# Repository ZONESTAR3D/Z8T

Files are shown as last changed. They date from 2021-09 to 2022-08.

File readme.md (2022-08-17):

# Z8T Documents
***ATTETION: We have released a new firmware for Z8T, please download it and upload to your printer, please refer to [here](https://github.com/ZONESTAR3D/Firmware/tree/master/Z8/Z8T/ZRIBV6(default)/Firmware/V2.0.0/LCD12864)***
### Download Z8T documents
[**Download all the Z8T documents in one go**](https://downgit.github.io/#/home?url=https://github.com/ZONESTAR3D/Z8T)     
## 0. Readme First
- **Packing list.jpg** Parts list of the Z8T 3D printer DIY kit    
- **Readme First.pdf** Installation and use process of 3D printer DIY Kit  
## 1. User Guide
- **Z8T User Guide-EN(FR/ES/PT/DE/RU).pdf**  Installation and quick user guide  
- **LCD2864 Menu Description.pdf** Menu instruction of 128x64 LCD screen    
- **LCD-DWIN Menu Description.pdf** MENU instruction of 4.3" TFT-LCD screen   
**NOTE**: Default Z8T used a 128x64 LCD screen, if you want to upgrade to a TFT-LCD screen, please refer to this link: [**Z8T upgrade kit**](https://www.aliexpress.com/item/1005002019863241.html)   
- **Z8T Wiring Diagram (ZRIBV6).jpg**  Wiring Diagram for Z8T  
- **TITAN installation tutorial.mp4**  Video tutorial for assemble TITAN extruder  
## 2. Operation Guide 
- [**Mix color HOTEND user guide- load and unload filament.pdf**](https://github.com/ZONESTAR3D/Z8T/blob/main/2.%20Operation%20Guide/Mix%20Color%20HOTEND%20User%20Guide-%20load%20and%20unload%20filament.pdf) Instrution for how to load and unload filament.  
- [**Operature guide for mixing color extruder.pdf**](https://github.com/ZONESTAR3D/Z8T/blob/main/2.%20Operation%20Guide/Operature%20guide%20for%20Mixing%20Color%20Extruder%20V1_3%20-EN.pdf)  Instrution for Operate the Mixing Color Extruder.   
**!!ATETTION!!: Please read these two document if you want to print multi-color 3d prints.**  
- [**Bed auto leveling**](https://github.com/ZONESTAR3D/Upgrade-kit-guide/tree/main/Bed%20Leveling%20Sensor) This directory has instructions on how to do the auto leveling and a leveling test gcode file.    
- **Host software** This directory contains instructions on how to control the 3d printer from PC  
- **Slicing** please click this link to read the newest [**slicing guide**](https://github.com/ZONESTAR3D/Slicing-Guide)  
- **USB driver** Default Z8T used a ZRIB control board, it used a CP2102 USB-UART briges chip, Please download the USB driver from here:
[**CP2012 USB Driver**](https://www.silabs.com/interface/usb-bridges/classic/device.cp2102)   
- **Upgrade features** You can upgrade some features for Z8T:
  - [**32 bits control board**](https://www.aliexpress.com/item/1005001300737027.html) > **Better performance**   
  - [~~**3.5" TFT-LCD with Touch screen**~~](https://www.aliexpress.com/item/1005001314076252.html) > Better UI - **Suggest upgrade to 4.3" TFT-LCD screen**
  - [**4.3" TFT-LCD screen**](https://www.aliexpress.com/item/1005002378065646.html) > **Better UI and easy to use**
  - [**Silent motor driver**](https://www.aliexpress.com/item/4000596369015.html) > **To make the printer more silent and improve printing quality**
  - [**Filament run out detector(FROD)**](https://www.aliexpress.com/item/4001309957376.html)  > **To detect filament run out and pause print**
  - [**3D Touch bed leveling sensor**](https://www.aliexpress.com/item/1005001464420529.html) > **Suit for all types hotbed.**
  - [**ZL-Sensor bed leveling sensor**](https://www.aliexpress.com/item/1005002865311470.html) > **Suit for all types of hotbed and easy to wiring.**
  - [**Hotbed Nuts**](https://www.aliexpress.com/item/4000726717520.html) > **Easy to adjust hot bed height** 
  - [**Magnetic flexible hot bed sticker**](https://www.aliexpress.com/item/4000793898821.html)  > **Pasted firmly and easy to take out**
  - [**Hotbed glass**](https://www.aliexpress.com/item/4001317243160.html) > **Print ABS required**       
  - [**Z lead screw fix module**](https://www.aliexpress.com/item/1005002401708373.html) > **Fix Z lead screws on the profiles**
  - [**The 4th version 3-IN-1-OUT hotend**](https://www.aliexpress.com/item/1005001635908007.html) > **Improve to less string and not easy to be clogged**  
  - [**3-IN-2-OUT hotend**](https://www.aliexpress.com/item/1005001275429959.html) > **make print different types of fialment and mixing feature together**  
  - [**3-IN-3-OUT hotend**](https://www.aliexpress.com/item/1005001275429959.html)  > **Support to print different filament**          
  - [**Upgrade parts combine**](https://www.aliexpress.com/item/1005002019863241.html)  > **Collection of most commonly used upgrade accessories**   
#### Use and installation guide for upgrade features, please refer to [here](https://github.com/ZONESTAR3D/Upgrade-kit-guide)  
- [**Bed Leveling Sensor**](https://github.com/ZONESTAR3D/Upgrade-kit-guide/tree/main/Bed%20Leveling%20Sensor)
	- [**PL-08N**](https://github.com/ZONESTAR3D/Upgrade-kit-guide/tree/main/Bed%20Leveling%20Sensor/Proximity%20Sensor%20(PL-08N))
	- [**ZLSensor**](https://github.com/ZONESTAR3D/Upgrade-kit-guide/tree/main/Bed%20Leveling%20Sensor/ZL-Sensor)
	- [**BLTouch**](https://github.com/ZONESTAR3D/Upgrade-kit-guide/tree/main/Bed%20Leveling%20Sensor/BLtouch(3D%20Touch))
- [**Direct Drive Extrruder**](https://github.com/ZONESTAR3D/Upgrade-kit-guide/tree/main/Direct%20Drive%20Extrruder)
- [**Filament run out sensor**](https://github.com/ZONESTAR3D/Upgrade-kit-guide/tree/main/FROD)
- [**HOTEND**](https://github.com/ZONESTAR3D/Upgrade-kit-guide/tree/main/HOTEND)
	- [**M2 2_IN-1-OUT Mixing Color Hotend**](https://github.com/ZONESTAR3D/Upgrade-kit-guide/tree/main/HOTEND/M2%202_IN-1-OUT%20Mixing%20Color%20Hotend)
	- [**M2P1 3-IN-2-OUT Mixing Color Hotend**](https://github.com/ZONESTAR3D/Upgrade-kit-guide/tree/main/HOTEND/M2P1%20%203-IN-2-OUT%20Mixing%20Color%20Hotend)
	- [**R3 3-IN-3-OUT HOTEND**](https://github.com/ZONESTAR3D/Upgrade-kit-guide/tree/main/HOTEND/R3%203-IN-3-OUT%20HOTEND)
	- [**M3 3-IN-1-OUT Mixing Color Hotend**](https://github.com/ZONESTAR3D/Upgrade-kit-guide/tree/main/HOTEND/M3%20%203-IN-1-OUT%20Mixing%20Color%20Hotend)
	- [**E4 4-IN-1-OUT Non-Mixing Color Hotend**](https://github.com/ZONESTAR3D/Upgrade-kit-guide/tree/main/HOTEND/E4%204-IN-1-OUT%20Non-Mixing%20Color%20Hotend)
	- [**M4 4-IN-1-OUT Mixing Color Hotend**](https://github.com/ZONESTAR3D/Upgrade-kit-guide/tree/main/HOTEND/M4%20%204-IN-1-OUT%20Mixing%20Color%20Hotend)	
- [**Laser Engraving Kits**](https://github.com/ZONESTAR3D/Upgrade-kit-guide/tree/main/Laser%20Engraving)
- [**Stepping motor drivers**](https://github.com/ZONESTAR3D/Upgrade-kit-guide/tree/main/Motor%20Drive%20Module)
- [**TFT-LCD screens**](https://github.com/ZONESTAR3D/Upgrade-kit-guide/tree/main/TFT-LCD)
	- [**3.5" TFT-LCD screen**](https://github.com/ZONESTAR3D/Upgrade-kit-guide/tree/main/TFT-LCD/TFTLCD35-MK)
	- [**4.4" TFT-LCD screen**](https://github.com/ZONESTAR3D/Upgrade-kit-guide/tree/main/TFT-LCD/LCD-DWIN)  
- [**WiFi wireless controller**](https://github.com/ZONESTAR3D/Upgrade-kit-guide/tree/main/WiFi)  
## 3. Test gcode
Inlcuded some gcode files for testing.  
## 4. TroubleShootings
Inlcuded some TroubleShootings files. 
## 5. Print Parts
Inlcuded the print parts stl fils for Z8T.
## 6. Firmware 
- [**Default firmware hex file**](https://github.com/ZONESTAR3D/Firmware/tree/master/Z8/Z8T/ZRIBV6(default)/Firmware/V2.0.0/LCD12864)     
- [**More Firmware hex file**](https://github.com/ZONESTAR3D/Firmware/tree/master/Z8/Z8T)  
- [**Firmware Upload tool (for windows)**](https://github.com/ZONESTAR3D/Firmware/tree/master/Firmware_Upload_tool_for_ZRIB_ZMIB)   
**NOTE: if you use macos and linux, please upload firmware by Cura**   
- [**Firmware sourc code**](https://github.com/ZONESTAR3D/source-code-for-3d-printer)

## How to downlod files from Github page
#### Step 1: Click this link [**https://downgit.github.io/**](https://downgit.github.io/) 
#### Step 2: Copy the Github file or direcotry link which you want to download.
#### Step 3: Click download button and wait a few seconds, it will start to download automatically. 


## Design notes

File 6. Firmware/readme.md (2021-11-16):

# firmware hex file
- please download from here: https://github.com/ZONESTAR3D/Firmware/tree/master/Z8/Z8T

# firmware source code
- please download from here: https://github.com/ZONESTAR3D/source-code-for-3d-printer

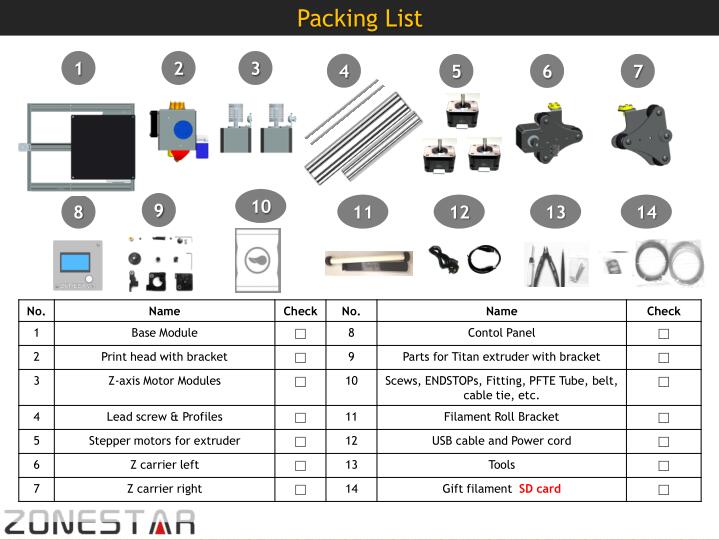
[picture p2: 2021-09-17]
0. Readme First/Packing List.jpg

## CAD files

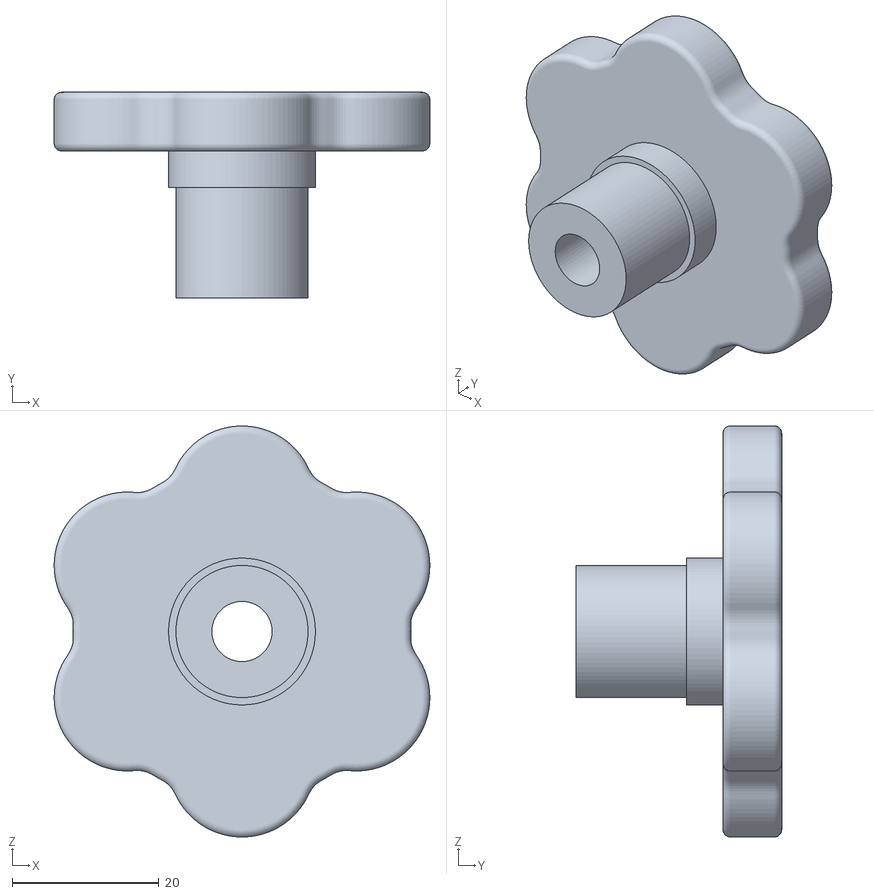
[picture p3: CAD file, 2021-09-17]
5. Print Parts/ls-cap.stl
51.2 x 28.0 x 56.0

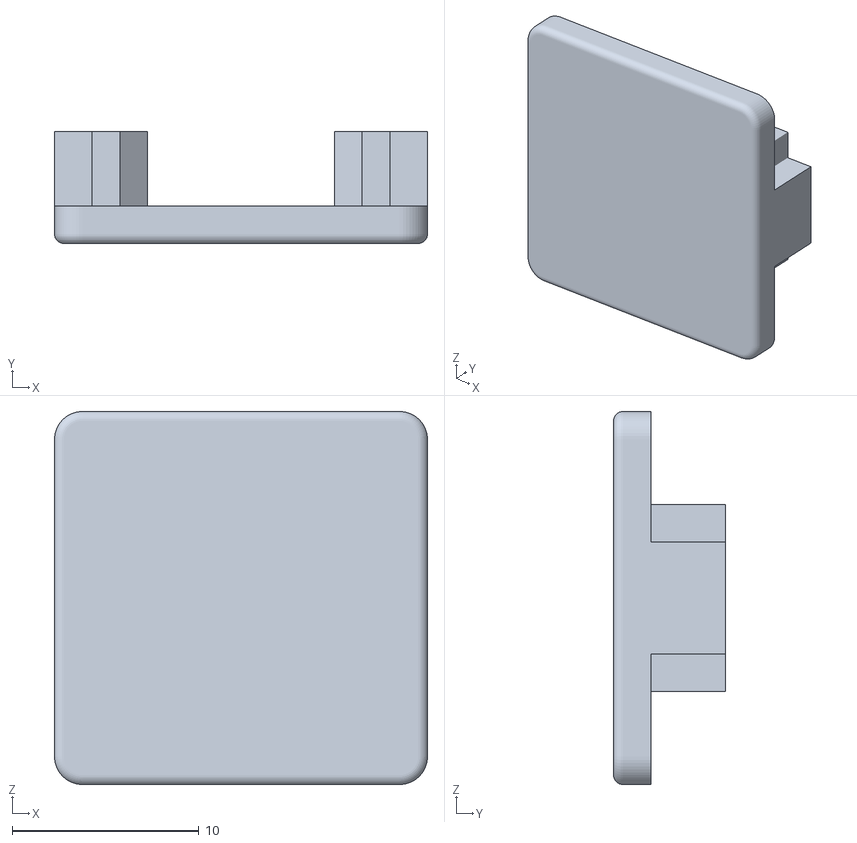
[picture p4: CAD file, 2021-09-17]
5. Print Parts/cap_af_20v.stl
20.0 x 6.00 x 20.0

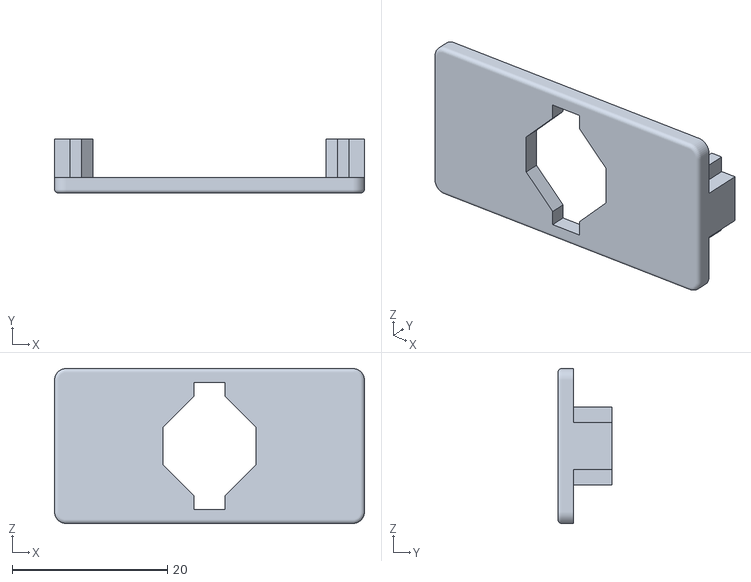
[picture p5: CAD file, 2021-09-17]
5. Print Parts/cap_af_40v.stl
40.0 x 7.00 x 20.0

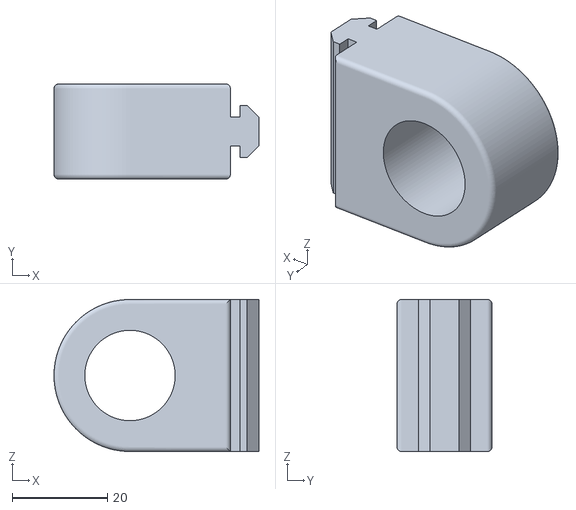
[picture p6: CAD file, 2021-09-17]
5. Print Parts/ls_hold.stl
43.1 x 20.0 x 32.0

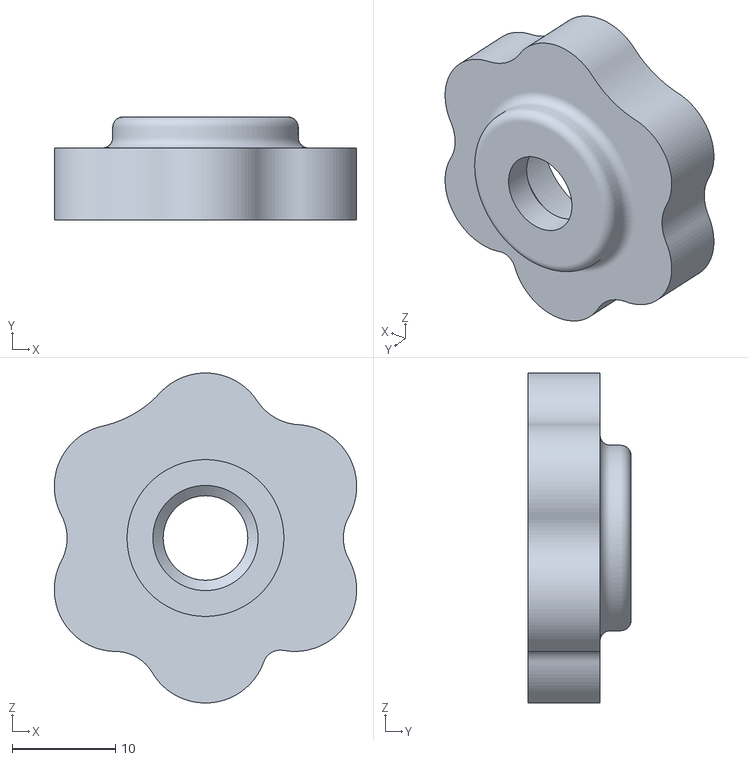
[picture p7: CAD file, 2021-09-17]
5. Print Parts/cap_m4nut.stl
29.3 x 10.0 x 32.0

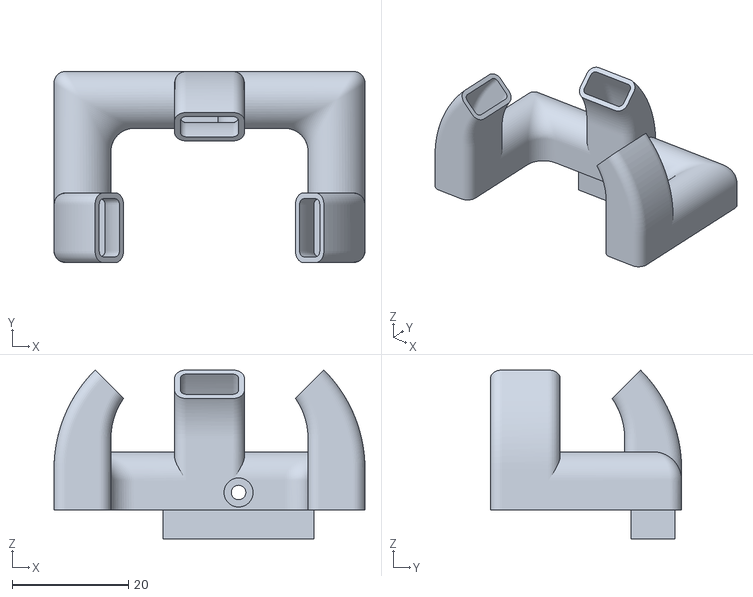
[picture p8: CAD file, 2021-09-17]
5. Print Parts/fanduck_m3_v4.stl
53.5 x 32.9 x 29.1

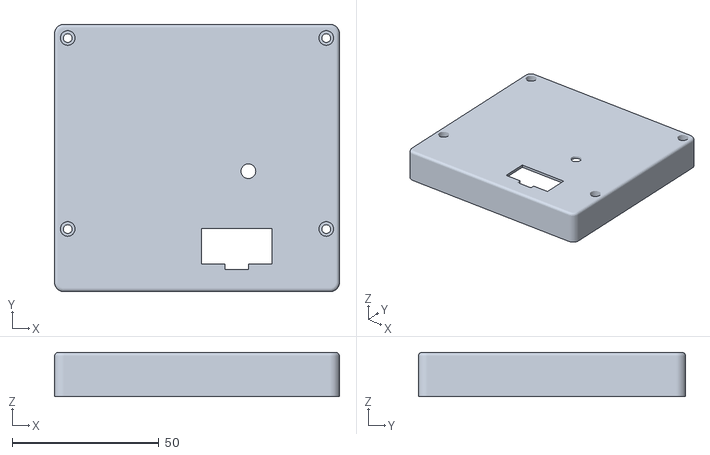
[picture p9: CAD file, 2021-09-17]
5. Print Parts/lcd12864_case_v2.stl
97.0 x 91.0 x 15.0

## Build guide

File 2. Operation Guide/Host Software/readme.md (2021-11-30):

If you want to control your 3d printer from PC, we recommend you choose repetier-host.  
[**Download Repetier host**](https://www.repetier.com/download-software/)
About how to use Repetier Host, please refer to "**Repetier Host User Guide V1.pdf**", more detail guide, please refer to [**Repetier-Host user guide**](http://www.repetier.com/documentation/repetier-host/)

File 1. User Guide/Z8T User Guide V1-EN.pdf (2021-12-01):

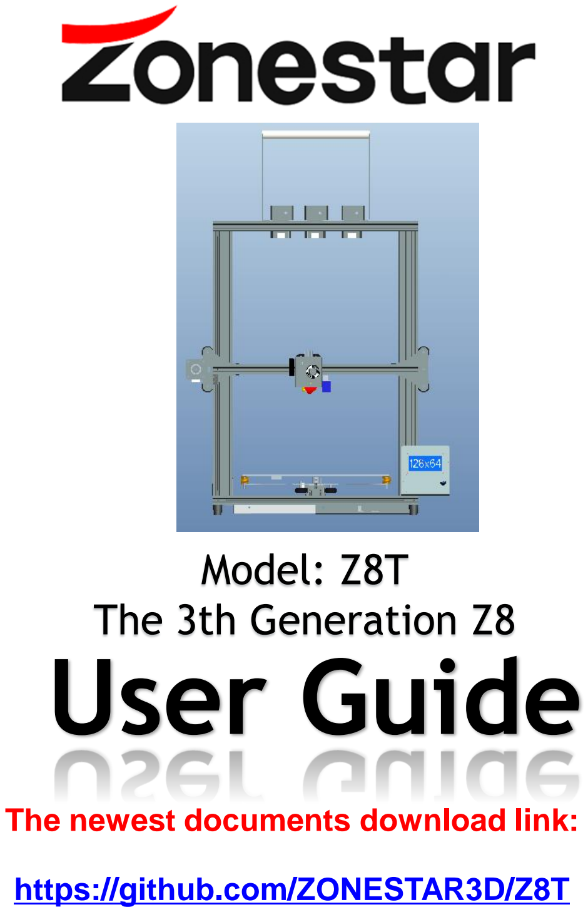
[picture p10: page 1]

# Model: Z8T The 3th Generation Z8

# User Guide

## The newest documents download link:

## https://github.com/ZONESTAR3D/Z8T

1、Nozzle diameter： | 0.4mm
2、Nozzle temperature: | 260℃max
3、Hotbed temperature: | 115℃max
3、Filament diameter： | 1.75mm
4、Print layer thickness: | 0.1~0.3mm(recommend 0.2mm)
5、Filament type: | PLA/ABS/PETG etc.
6、Slicing software： | Cura/Repetier-Host/Simplify3D
7、Interface mode： | USB/SD-Card
8、Power specifications： | Input: 100VAC or 240VAC,50/60Hz
| Output: 24V,15A
9、Print size： | 300(X)*300(Y)*400(Z)mm
10、Gross weight： | 12Kg
11、Environment temperature: | 5~40℃

# Symbols

•Extruder:
The system to carry out Feeding-Melting-Stacking in FDM 3d printer. •Extrusion feeder:
A mechanism to transport filament to the hot end.
•Titan Extruder:
A special remote extrusion feeder with deceleration structure, it can reduce the torque requirements in the stepper motor. •3D printer filament:
In order to facilitate the work of 3D printer, plastic materials are pre processed into filaments. The commonly used types include PLA, ABS, PETG, TPU, PC, AAS, HIPS, PVA, WOOD, Carbon Fiber, etc..
•Hotend:
The part to melt the filament.
•Nozzle:
The outlet at the front end of the HOTEND, usually made of copper and has a small size hole for flow out filament. •Print head:
It means the Hotend and its attached cooling system.
•Printing platform:
The device supporting the printed object.
•Hotbed:
Heatable printing platform.
•Sticker (of hotbed):
A special stickers pasted on the Hotbed are usually made of high temperature adhesive tape or PC film. •Bed Automatic leveling:
A function of automatically measuring and adjusting the distance between nozzle and printing platform. •Control panel:
The system that realizes human-machine interface in 3D printer.
•CoreXY:
A special motion structure with two motors and belt to drive the X-axis and Y-axis together, it is appiled in Z9M3. •Motor Driver Module:
An electronic function module to drive stepper motor.
•Mixer:
The parts and software to realize the color mixing function.
•HOTEND Clean tool:
A screw with a small rod which can be used to clean the feeding channel at the hot end or close the unused channel.

Please put the printer away from the reach of kids.

Must be guided by adults when children are installed or used.

Take care when installation, to avoid electrical shock hazards.

## Please keep well-ventilated condition! May produce toxic gases when

printer working.

## Caution: Hot!

Hotend has high temperature even the printer stop working.

## Caution: Hot!

Hotbed has high temperature even the printer stop working.

Please strictly follow the standard operation when installation.

## Please make sure you have set the AC power select switch to the

correct position before power on.

## For mixing color printer, must load filament to all of the extruders or use hotend clean tool to close the unused channel, even if you print

single color 3D object.
4

# Packing List

1 | 2 | 3 | 4 | 5 | 6 | 7

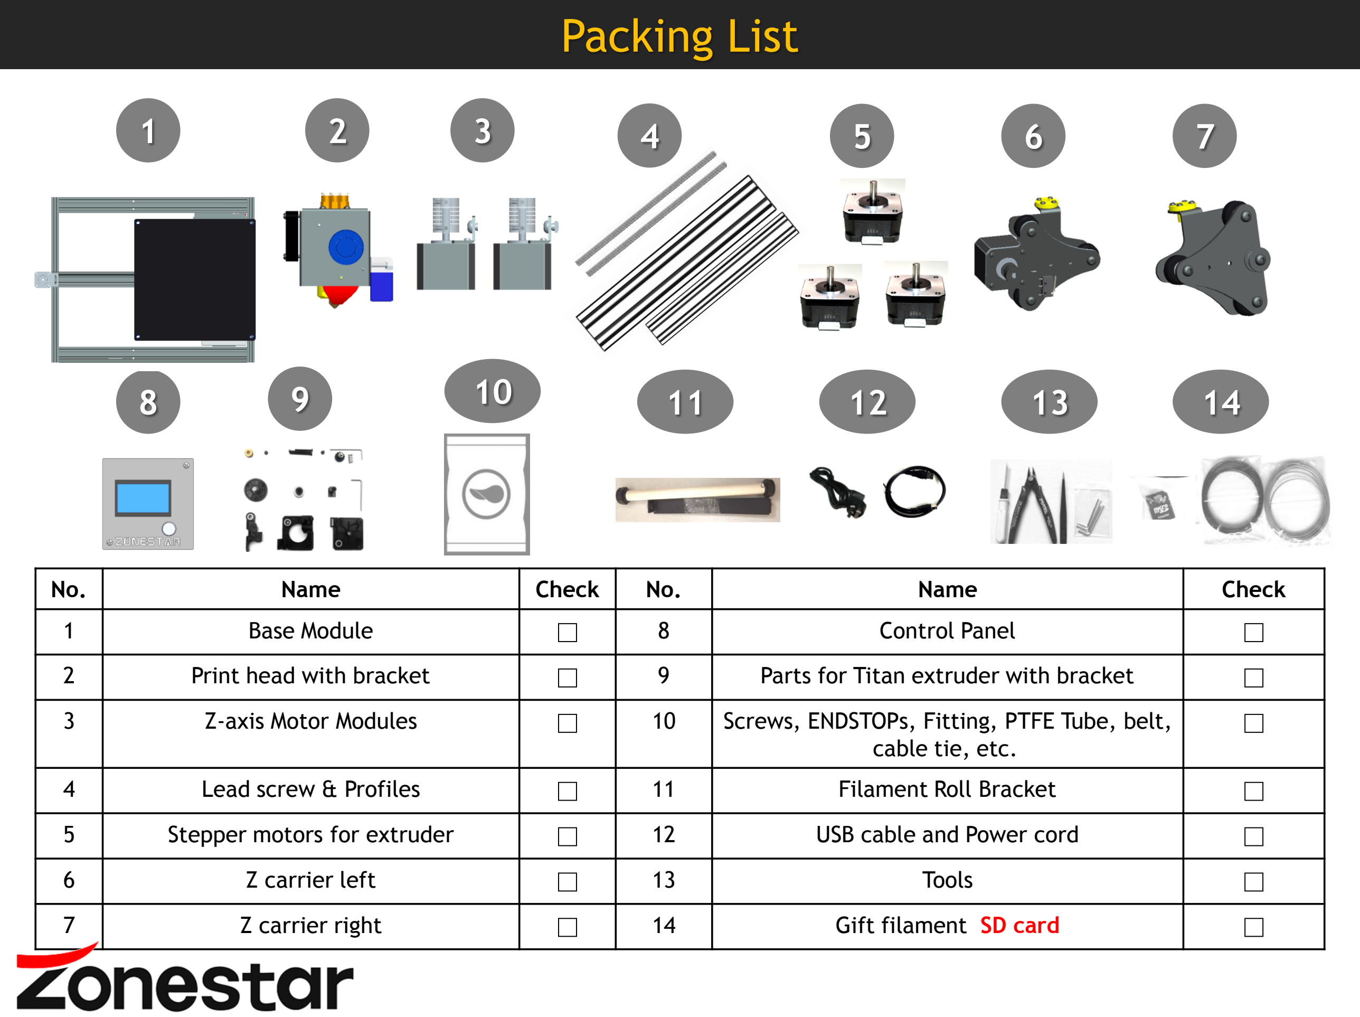
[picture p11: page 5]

No. | Name | Check | No. | Name | Check
1 | Base Module | □ | 8 | Control Panel | □
2 | Print head with bracket | □ | 9 | Parts for Titan extruder with bracket | □
3 | Z-axis Motor Modules | □ | 10 | Screws, ENDSTOPs, Fitting, PTFE Tube, belt, cable tie, etc. | □
4 | Lead screw & Profiles | □ | 11 | Filament Roll Bracket | □
5 | Stepper motors for extruder | □ | 12 | USB cable and Power cord | □
6 | Z carrier left | □ | 13 | Tools | □
7 | Z carrier right | □ | 14 | Gift filament SD card | □

8 14

9 | 11 | 12 | 13 10

# Assemble Titan Extruder (3 sets)

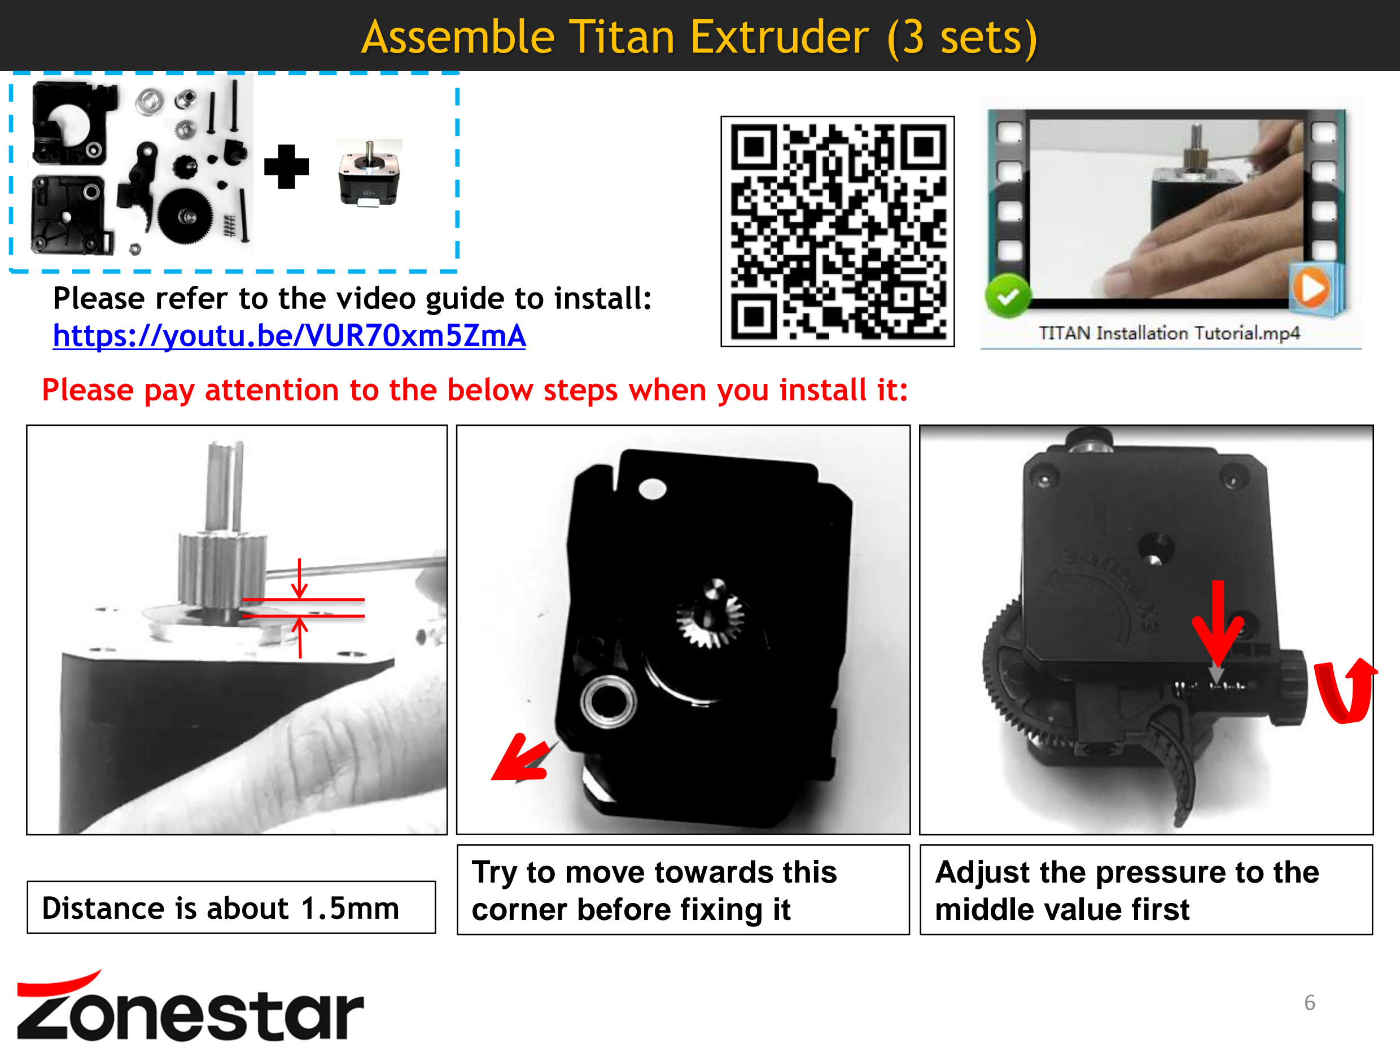
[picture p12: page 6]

## Please refer to the video guide to install: https://youtu.be/VUR70xm5ZmA

## Please pay attention to the below steps when you install it:

## Try to move towards this Distance is about 1.5mm corner before fixing it

## Adjust the pressure to the middle value first

# Install Z axis Parts

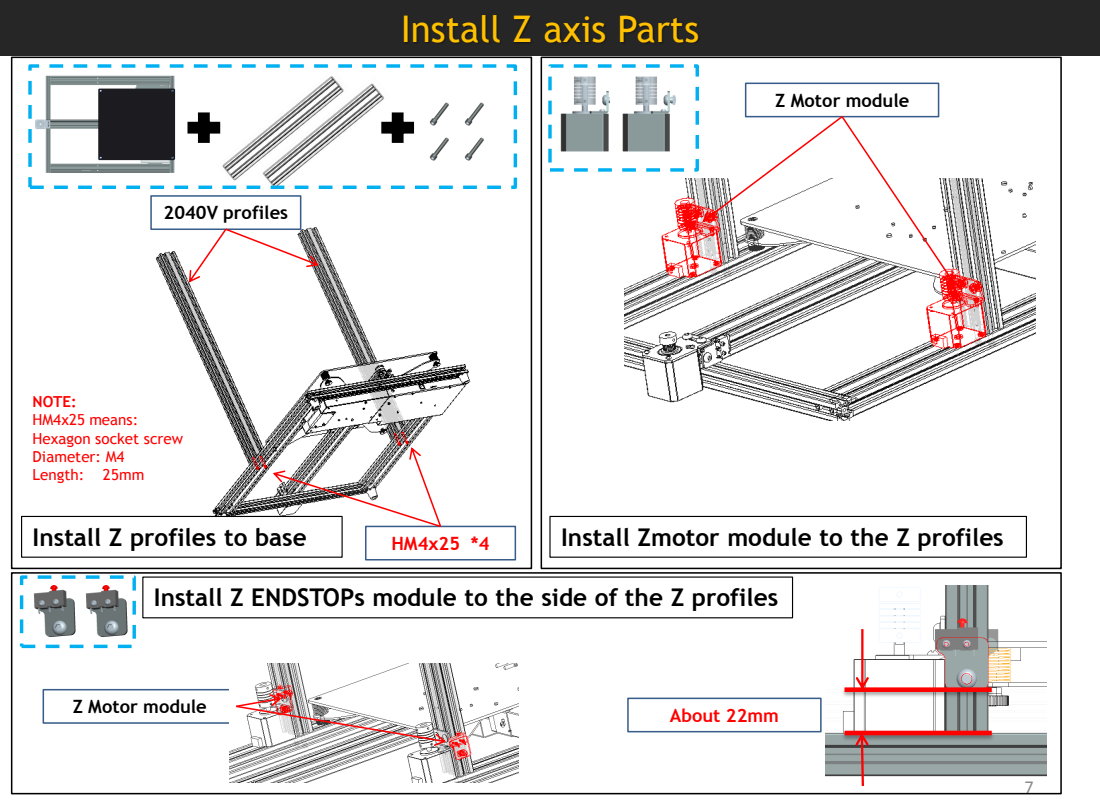
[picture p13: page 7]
2040V profiles; Z Motor module; About 22mm; Length:

NOTE:
HM4x25 means:
Hexagon socket screw
Diameter: M4

Install Z profiles to base

Install Zmotor module to the Z profiles

Install Z ENDSTOPs module to the side of the Z profiles

# Install Z axis Parts

Install Z silders | Install lead screws

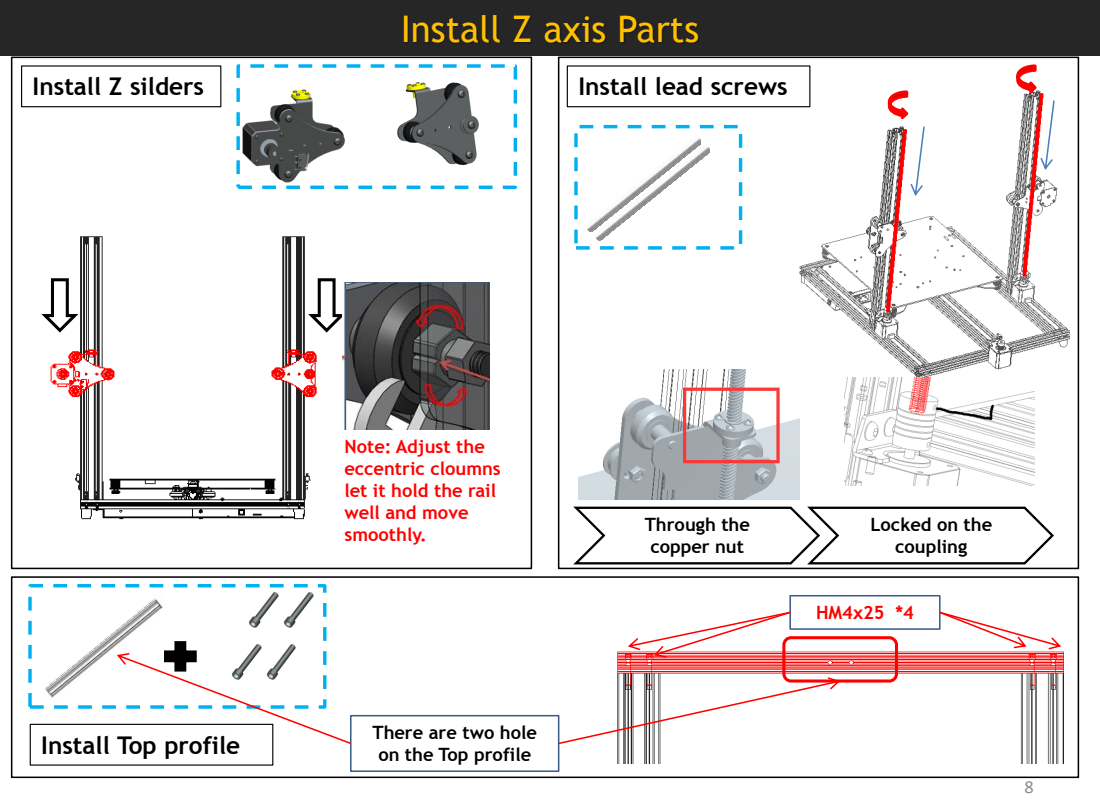
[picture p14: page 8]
Through the copper nut

Note: Adjust the
eccentric cloumns
let it hold the rail
well and move
smoothly.

Locked on the
coupling

There are two hole
on the Top profile

Install Top profile

# Install X axis Parts

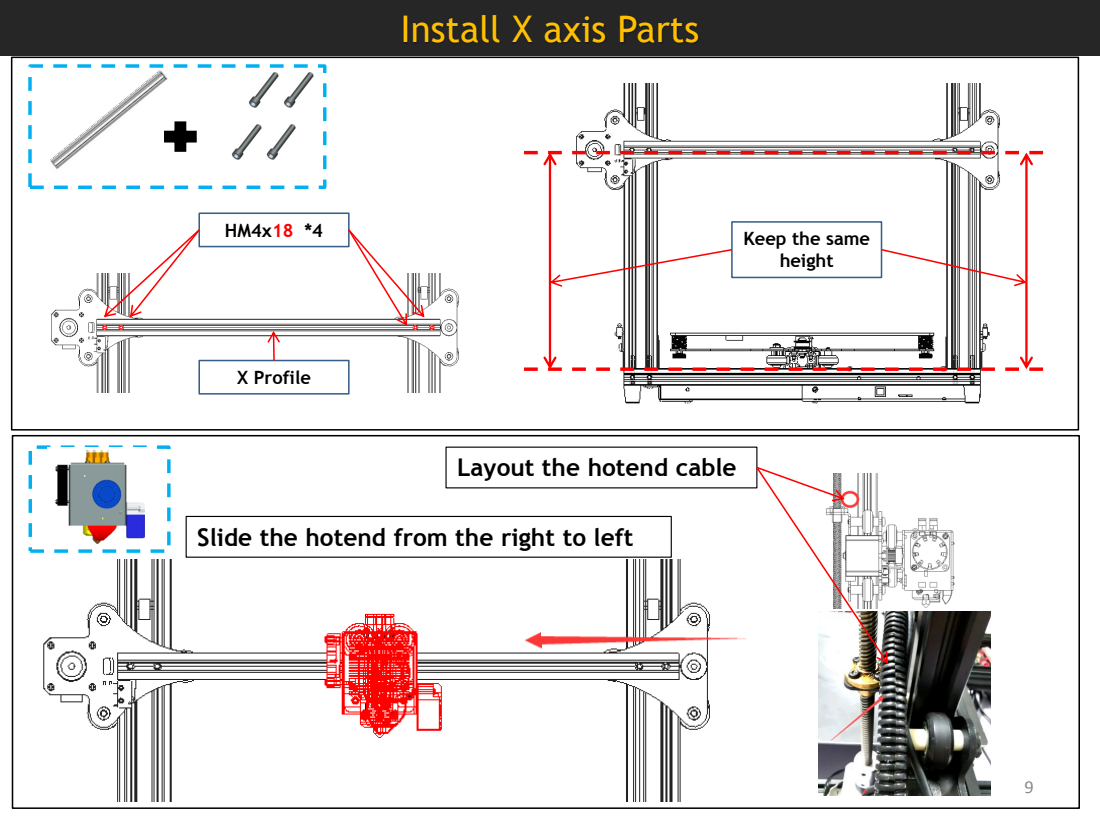
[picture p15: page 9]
X Profile

Keep the same
height

Layout the hotend cable

Slide the hotend from the right to left

# Install X belt

## Install the X belt

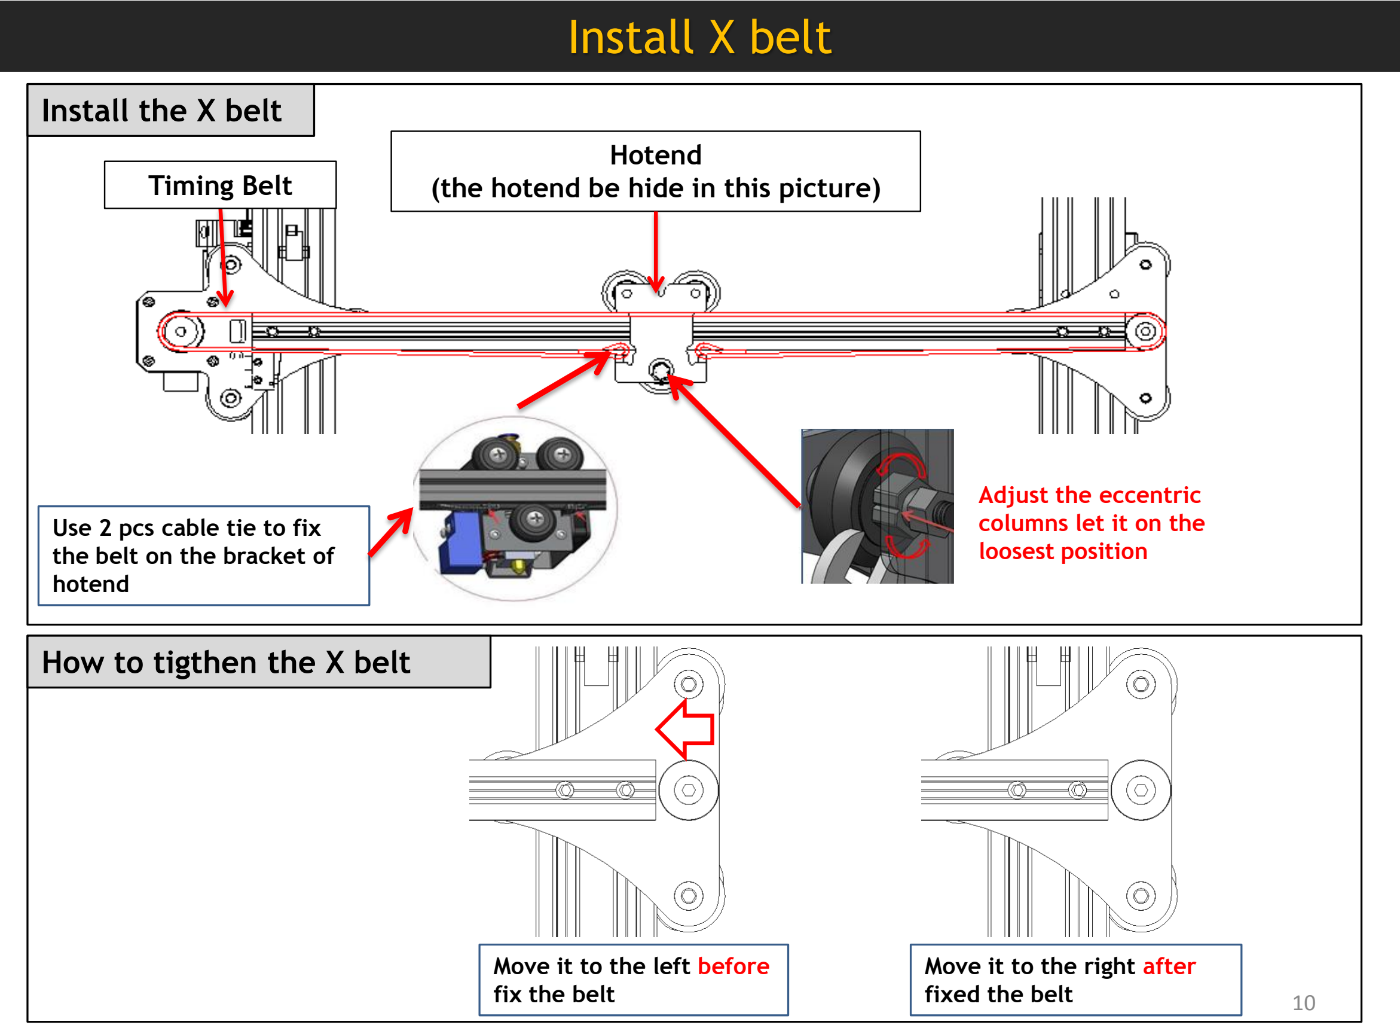
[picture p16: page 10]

Timing Belt

Hotend
(the hotend be hide in this picture)

Adjust the eccentric
columns let it on the
loosest position

Use 2 pcs cable tie to fix the belt on the bracket of hotend

Move it to the left before fix the belt

Move it to the right after fixed the belt

## How to tigthen the X belt

# Install the other parts

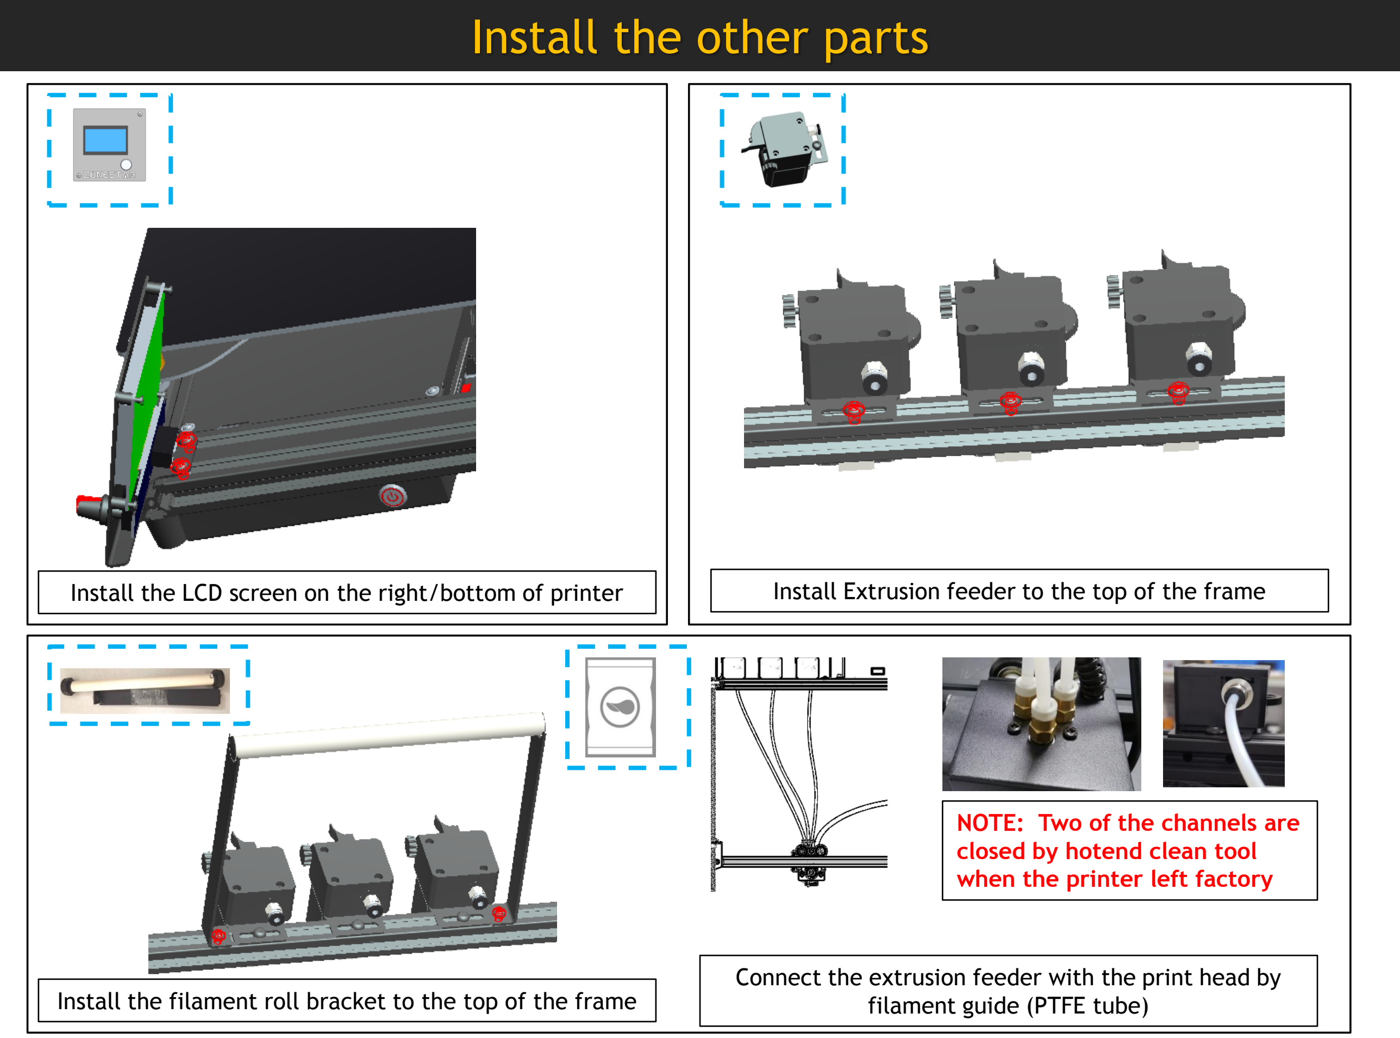
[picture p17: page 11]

Install the LCD screen on the right/bottom of printer | Install Extrusion feeder to the top of the frame

Install the filament roll bracket to the top of the frame

Connect the extrusion feeder with the print head by filament guide (PTFE tube)

NOTE: Two of the channels are closed by hotend clean tool when the printer left factory

# Adjust height of Z ENDSTOPs

## Step 1: Adjust the 4 hand nuts under the hotbed, let the hotbed is parallel with bottom

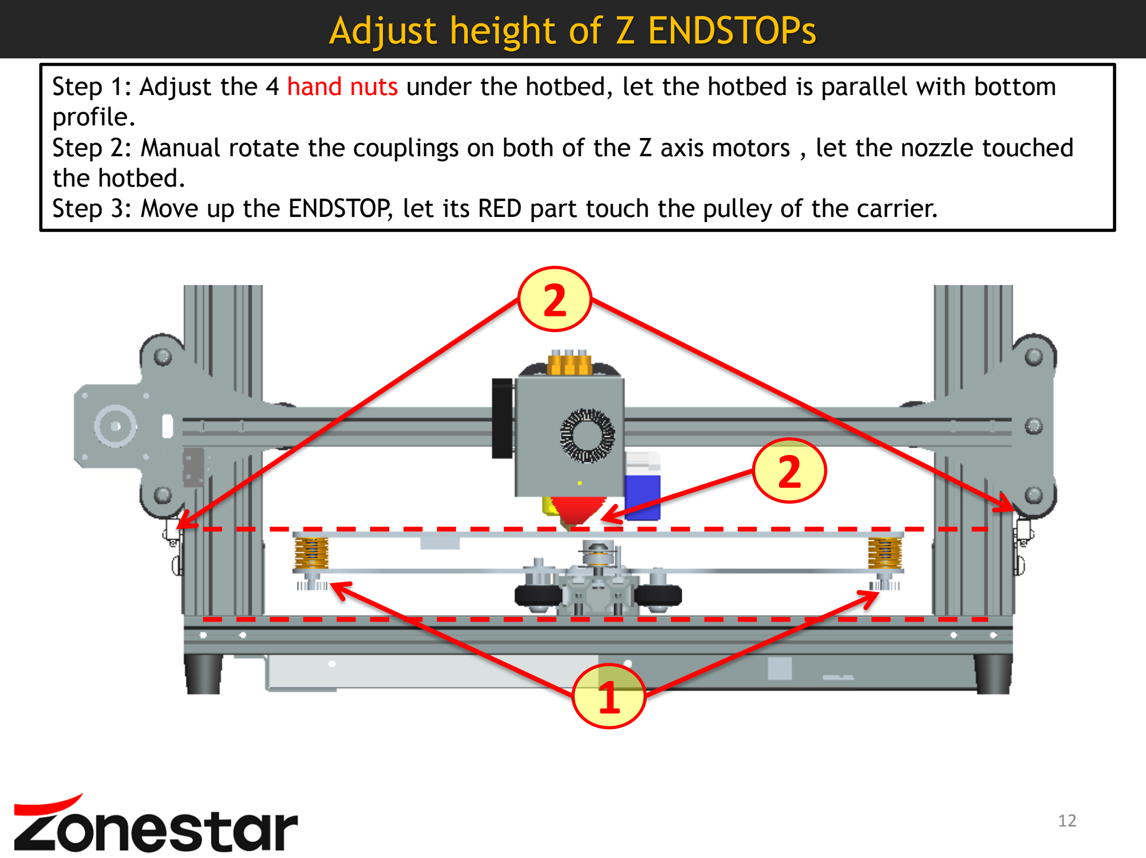
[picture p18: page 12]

profile.

## Step 2: Manual rotate the couplings on both of the Z axis motors , let the nozzle touched

the hotbed.
Step 3: Move up the ENDSTOP, let its RED part touch the pulley of the carrier.

1

2

2

# !!ATTENTION!!

## Take care when installation, to avoid electrical shock hazards!

## Double check the wiring! WRONG WIRING MAY DAMAGED THE ELECTRONIC DEVICE!

## Set the 110V/220V swicth (on the side of power supply) to correct position according to your city power voltage!

## Put the motor wire to the grooves of profile and cover them by

plastic profile cover, and using cable tie to wrap the free wires.

## Stop working immediately if the motor has abnormal vibration or noise,, otherwise the driver modules may be damaged!

## Make sure the hotend cooling fan is working when the nozzle

temperature is over 60 degree, otherwise check the wiring again.

## DC-IN, HOTBED has lager operating current, please make sure

these wires contact well with the terminal.

Step 4: Manually move the hotend and hotbed to see if the movement is smooth, otherwise,

## adjust the eccentric nut until the motor moves smoothly. Refer to the installation

procedure.

## Step 3: Move the hotend and hotbed to their respective limit switch positions to check whether the contact is good and there is a clear sound. Otherwise, please check the limit

switch and reassemble it.

## Step 7: Manually rotate the z-axis screw rod to check whether the z-axis limit switch

contacts reliably.

Step 5: Check whether the X and Y-axis drive belt is firmly installed. If it is too loose, please try to tighten it.

## It is very important to check the machine before power on. It can eliminate the trouble brought by some hardware to ensure the smooth printing!

## Step 6: Check whether the screw rod is assembled in place and whether the screw is tightened

Step 1:Please check if the X&Y axis timing pulley are fixed on the shaft of motor, and the couplings are fixed on the shaft of the Z motors.
Step 2:Please check if the lead screws have been fixed on the shaft of coupling.

# About electronics parts

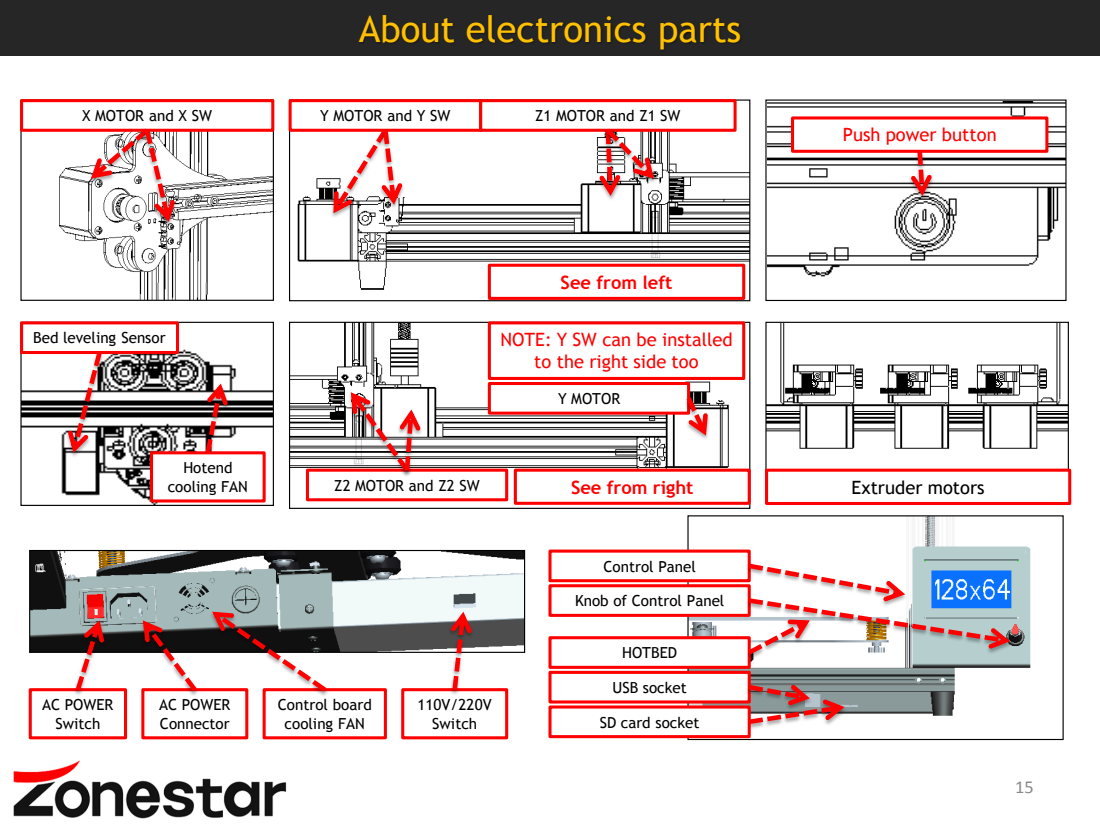
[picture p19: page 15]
X MOTOR and X SW; Y MOTOR and Y SW; Z1 MOTOR and Z1 SW; Extruder motors; Hotend; cooling FAN; Z2 MOTOR and Z2 SW; Y MOTOR; AC POWER Switch; AC POWER Connector; Control board cooling FAN; 110V/220V Switch

Push power button

See from left

Bed leveling Sensor

NOTE: Y SW can be installed
to the right side too

See from right

Control Panel

Knob of Control | Panel

HOTBED

USB socket

SD card socket

# Wiring photos

## Before power on, please open the control box and double check the wiring:

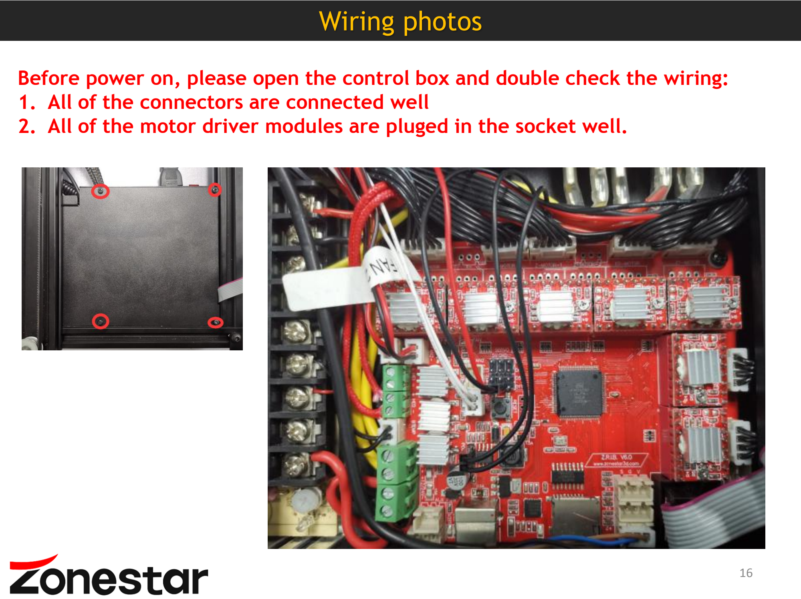
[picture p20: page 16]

## 1. All of the connectors are connected well

2. All of the motor driver modules are pluged in the socket well.

# Wiring Diagram

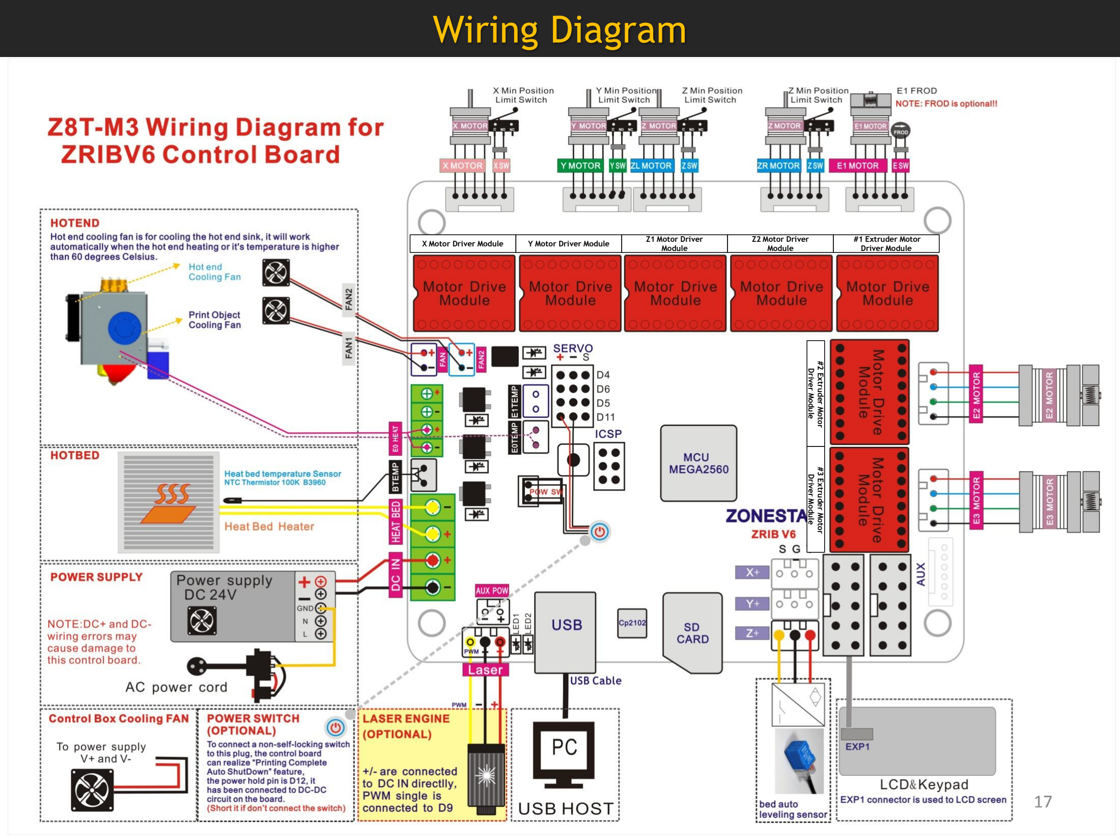
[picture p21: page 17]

X Motor Driver Module | Y Motor Driver Module | Z1 Motor Driver Module

Z2 Motor Driver
Module

#1 Extruder Motor

Driver Module

#2 Extruder Motor

Driver Module

#3 Extruder Motor

Driver Module

# Layout the wires / cables

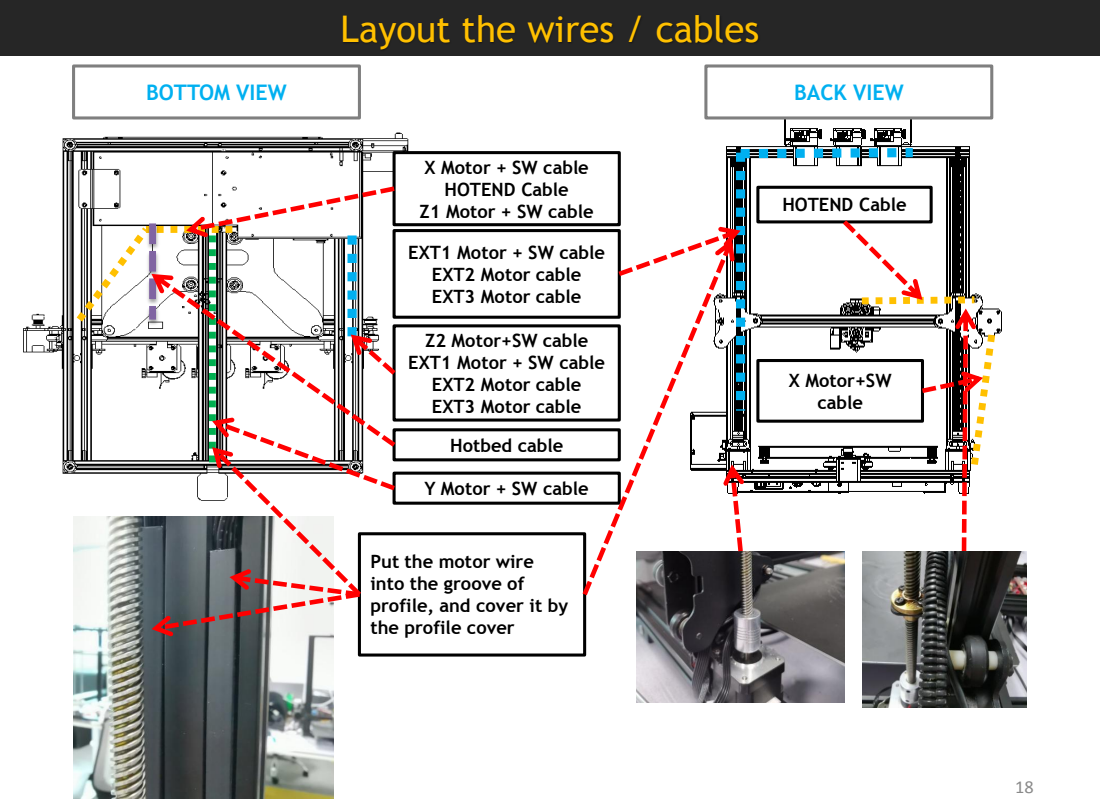
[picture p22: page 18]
Hotbed cable; BOTTOM VIEW; BACK VIEW; HOTEND Cable; X Motor+SW cable

X Motor + SW cable
HOTEND Cable
Z1 Motor + SW cable

EXT1 Motor + SW cable
EXT2 Motor cable
EXT3 Motor cable

Z2 Motor+SW cable

Y Motor + SW cable

Put the motor wire
into the groove of
profile, and cover it by
the profile cover

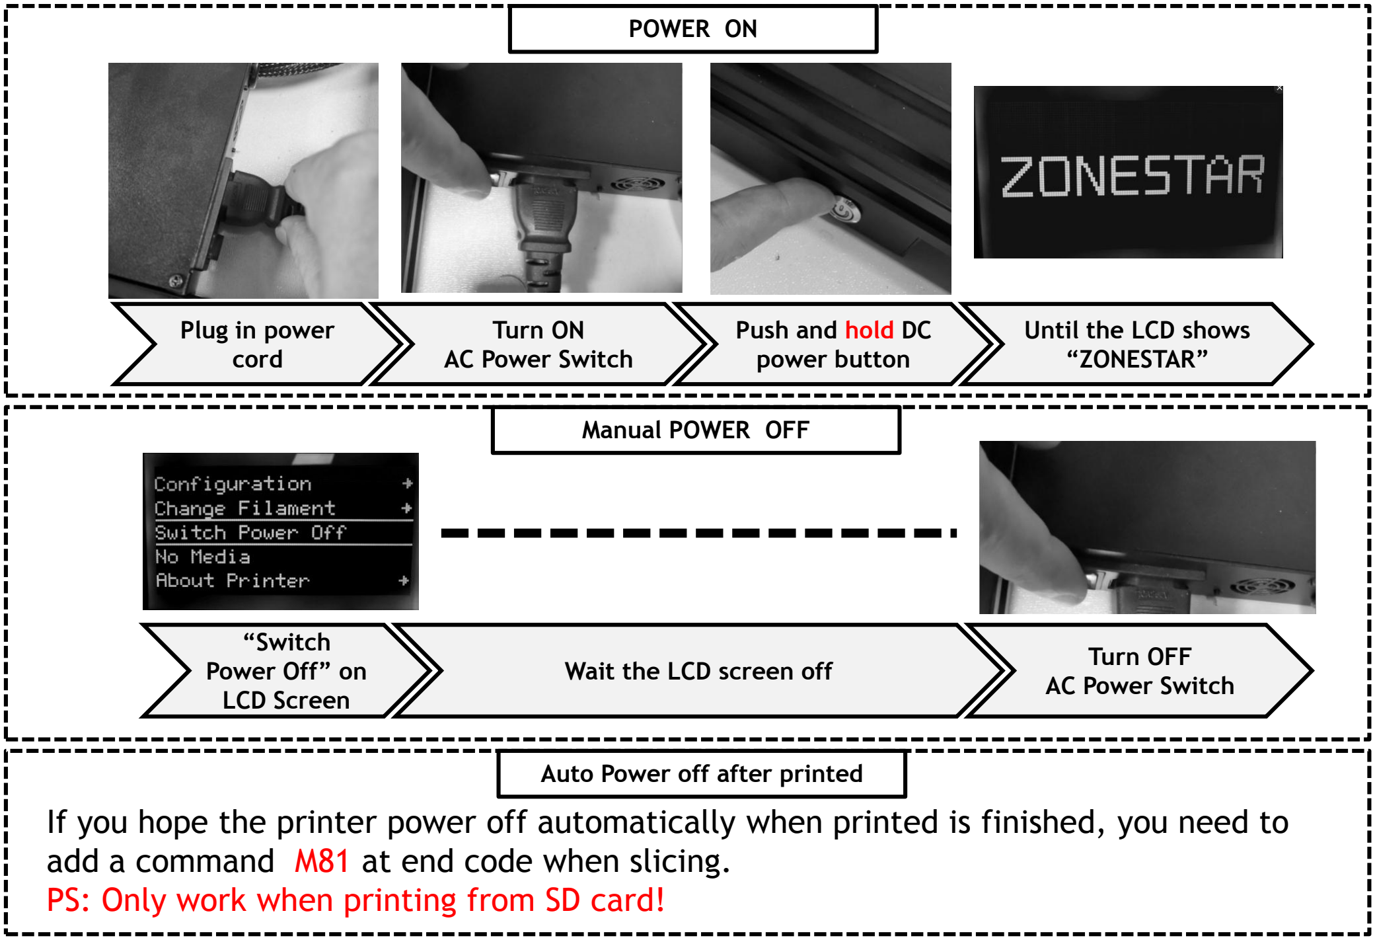
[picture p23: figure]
Wait the LCD screen off; Manual POWER OFF; “Switch Power Off” on LCD Screen; Turn OFF AC Power Switch; Plug in power cord; Turn ON AC Power Switch; Push and hold DC power button; Until the LCD shows “ZONESTAR”; POWER ON; Auto Power off after printed

## If you hope the printer power off automatically when printed is finished, you need to

add a command M81 at end code when slicing.

## PS: Only work when printing from SD card!

## Knob operation: <Clockwise rotation>: Next Item / Value +. <Counterclockwise rotation>:

Previous Item / Value -. <Push>: Enter / Execute.

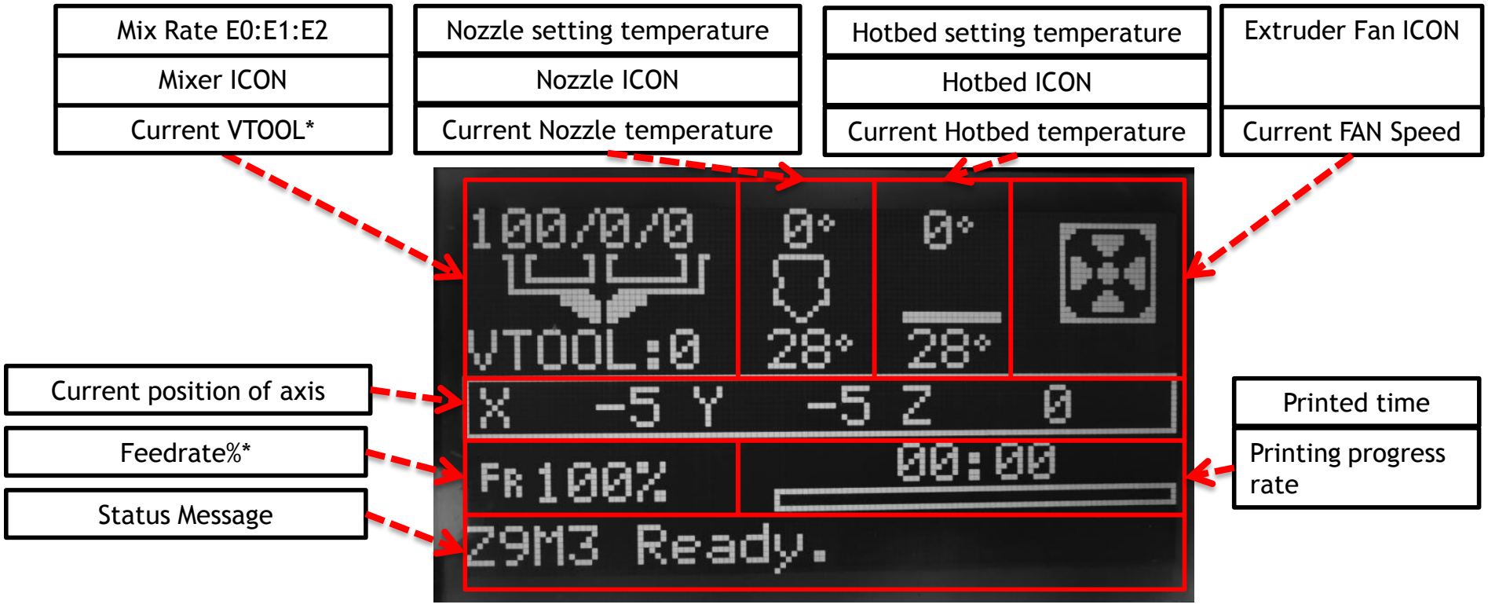
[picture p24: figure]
Status Message; Printed time; Printing progress rate; Extruder Fan ICON; Current position of axis; Feedrate%*; Current VTOOL*; Mix Rate E0:E1:E2; Mixer ICON; Nozzle setting temperature; Nozzle ICON; Current Nozzle temperature; Hotbed setting temperature; Hotbed ICON; Current Hotbed temperature; Current FAN Speed

For details on the LCD menu, please refer to "LCD Menu Description.pdf".

VTOOL: In singel color or general multicolor printer, each extrusion motor corresponds to one nozzle, then one extruder + one nozzle constitutes one tool chain; In mixing color extruder, multiple extrusion motors correspond to one nozzle. Setting different rotation ratios of extrusion motors can form multiple virtual tool chains.M3 extruder can set up to 16 VTOOLs. About detail, please refer to “Mixing Color Hotend User Guide.pdf”
Feedrate: When printing from an SD card, adjusting the feedrate can adjust the printing speed, it is based on
the speed set by the gcode file when slicing. | 20

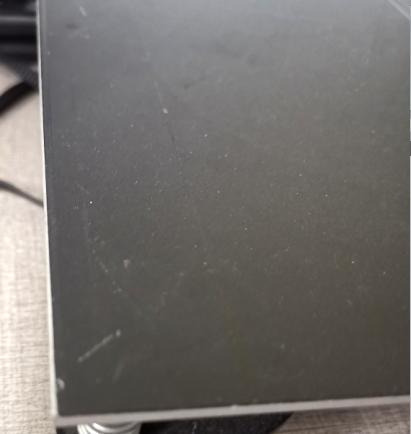
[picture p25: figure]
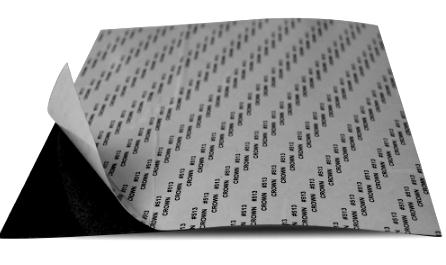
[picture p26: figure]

Remove the paper | Paste on the hotbed

## NOTE:

Take care when pasting, avoid the influence of air bubbles cause the hot bed is not smooth.

## Tips:

First tear off one side of the sticker on the back, then Level with a shovel from one side to the other side, and then gradually tear off the sticker on the back.

After finish to assemble and wiring, please following the steps below to verify.
Step 1: Before turning on the power, confirm again:
✓ | Check if it has been set correctly of the 110V/220V power voltage select switch.
✓ | Check if the components are connected correctly. Especially, DC+ and DC- of the DC power didn't reverse, the wiring is in good
| contact with the terminals and no wires are shorted.
✓ | Check if the cable of LCD is connected well to EXP1 connector.
Step 2: Check temperature sensor:

Plug in the AC power cord and turn on AC power, watch the LCD screen, temperature should be almost the same with ambient temperature.
Step 3: Check X, Y and Z axis Motors and ENDSTOPS:

DO: Motion>>Move axis>>Move X/Y/Z>> Move 10mm. Enter and rotate knob to move the X/Y/Z axis.

CHECK: Check if the print head can move left/right (X axis), front/back (Y axis), or the hotbed can move up/down (Z axis).

| NOTE: If the X and Y can’t move correctly, e.g. when moving X or Y, the print head move in 45 degrees, it means that x motor or Y motor does not working, please check the wiring.

CHECK: Press and hold the X/Y limit switch, and try to reduce the value of Move X/Y, the print head should stop moving, otherwise check
| the connection of the X/Y limit switch.

CHECK:Press and hold the Z limit switch, and try to reduce the value of Move Z, the hotbed should stop moving, otherwise check the
| connection of the Z- limit switch.

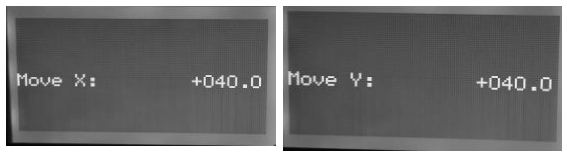
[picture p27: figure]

Step 4: Check heaters and Fans:
1. Temperature>>Nozzle: 180, set the nozzle temperature to 180 degrees, and then return to info menu, the nozzle temperature will rise, usually it is one degree per seconds or so.
2. Temperature>>Bed: 60, set the heat bed temperature to 60 degrees, and then return to info menu, the hotbed temperature will rise, usually it is one degree per 2 seconds or so.
3. Check HOTEND cooling fan. When the nozzle temperature is over 60 degrees, the cooling fan on the side of print head should work.
4. Check Extruder fan, Temperature>>Fan Speed: 100%, the extruder fan should work.

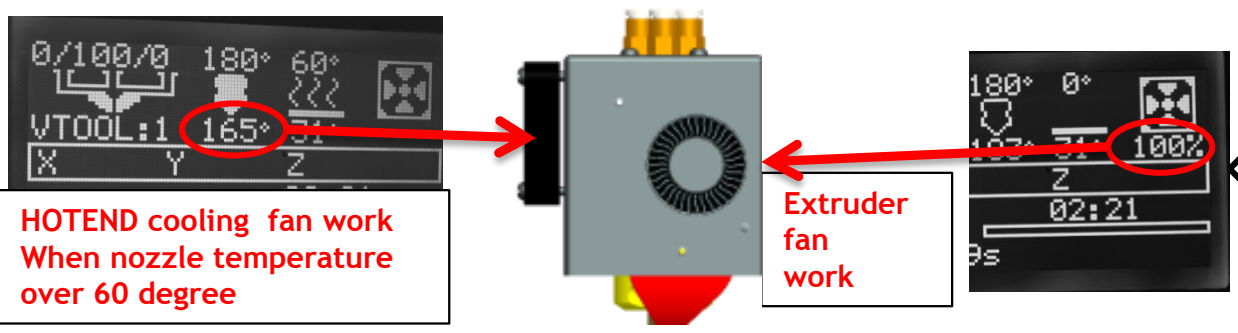
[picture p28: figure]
Extruder fan work; HOTEND cooling fan work When nozzle temperature over 60 degree

Step 5: Check extrusion feeders:
1. Temperature>>Nozzle: 180, set the nozzle temperature to 180 degrees, and then return to info menu, waiting for the temperature reached to the setting.

### 2. Set the mixing ratio of all extruders to the same (33:33:34):

Mixer>>Set Mix>>Active V-tool: 0>> set to Active V-tool: 3
3. Move Axis>>Extruder>>Move 10mm>>Extruder: +20mm, watch the gear of the extrusion feeder, and check if all of the extrusion feeders will work.

# Quickly Trouble-shooting

LCD does not display after Power on | 1. The backlight of LCD does not light up. Possible reasons: The AC power cord is not plugged in; DC+ and - are reversed; the power socket are disconnected with power supply. 2. The backlight of LCD light but has not characters. Possible reasons: LCD cable is reversed; firmware error or lost;

Error temperature

Motor or extrusion feeder does not work properly | 1. The power supply does not work (Note:USB can also supply +5V power and let the LCD display, but can not supply power to the motors and heater). 2. The motor cable is disconnected. 3. The motor drive module didn’t connect well with the socket of control board. 4. Heating the nozzle to over 150 degrees before extruding.
Error Motor Direction | 1. The motor is not connected to the correct connecotor of the control board, such as exchanged the X and Y sockets. 2. The wire sequence of the motor cable is incorrect. 3. The firmware version is incorrect.
Issue of limit switch(ENDSTOP) | 1. The wire of the limit switch is disconnected to the control board. 2. The limit switch is connected to the wrong connector, for example, exchanged the X and Y limit switches. 3. The wire is disconnected witht the limit swich. 4. Check the singnal of the limit swith, it should be connected to pin “S” and “GND” of the connnector on control board.
Issue of heatbed and hotend | 1. The printer reboot automatically when heating the heat bed or nozzle. Check if the AC power supply voltage selection switch is set correctly and the DC power cable is connected well. 2. Hotend cannot be reached to the setting temperature. Check if the thermistor is missing from the heated block. Check if the printhead heater cable is connected well. 3. Hotbed cannot be reached to the set temperature. A)Check if the wiring is contact well. B)Check If the ambient temperature is less than 5 degree.

Hotend temperature sensor
doesn’t connect well

Hotbed temperature sensor
doesn’t connect well

Clean nozzle: make sure there aren't any filament at the end of nozzle, if not, remove it by a diagonal pliers. 1

2

3

Choose “Motion>> Auto Home”>>, wait the hotend go to the orig position.

Watch the nozzle and make sure the nozzle is higher than the bed, otherwise tighten the hand nuts under the bed to pull down the hotbed or loosen these nuts to move up the bed.

4

Choose “Motion>> Level Corners”>>, the nozzle will go to the corners, adjust the hand nuts under the hotbed, let the nozzle almost touch the hotbed. In order to get a properly distance, you can put a A4 paper on the hotbed, and when the distanse between the nozzle and hotbed can only insert a paper, it will be perfect.

Choose “next corner”, and adjust again. Repeat this step again and again, until all of the four corner at the same height. 5

Preheat nozzle: Temperature>> Nozzle, set it to about 180 degree (for PLA) or 220 degree(for ABS and PETG filament), then nozzle will be heated. Waiting nozzle temperature reached to setting.

1

2

Press the handle on the extrude feeder and insert filament, until the filament enter to the hotend.

Choose “Motion>> Move axis>>Extruder>>Move 1mm>>extruder: ****mm”, then Clockwise rotate the knob slowly, until you can see the filament is flowed from the nozzle. 3

## NOTE: We strongly recommend that you start with single color. When the product leaves the factory, we have closed two channels with two hotend cleaning tools. You can use the channel that is not closed to print your first works!

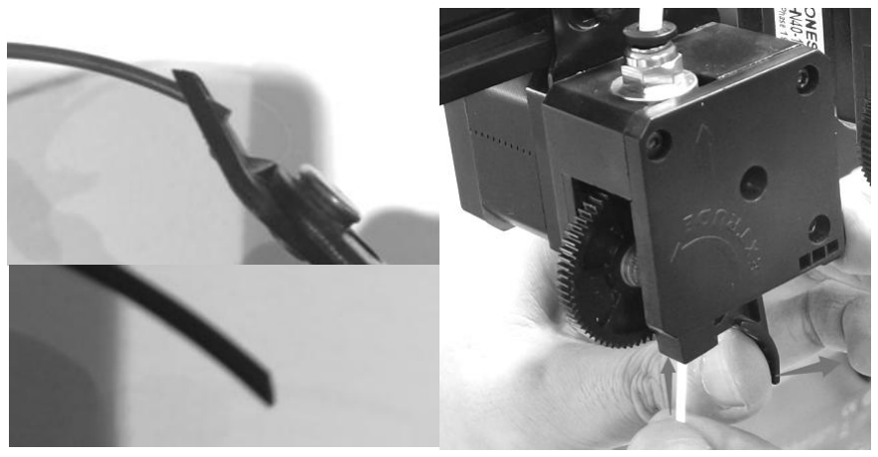
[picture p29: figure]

# Print a test 3D object (Print from SD card)

1 Insert the SD card to the SD card socket on the control box, and then power on the control box.

2

Choose “Print from Media>>Test_gcode\Single Color\xyz_cube.gcode”, push the knob to start printing.

3

Wait the printer to finish heating and start to print, watch the distance from nozzle to bed, double click the knob of LCD menu and set the z offset if the distance is not perfect, let the filament can stick on the hotbed well.

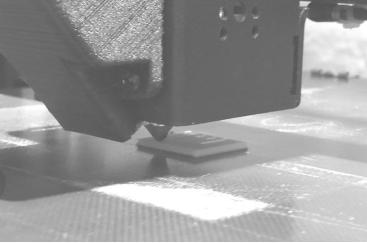
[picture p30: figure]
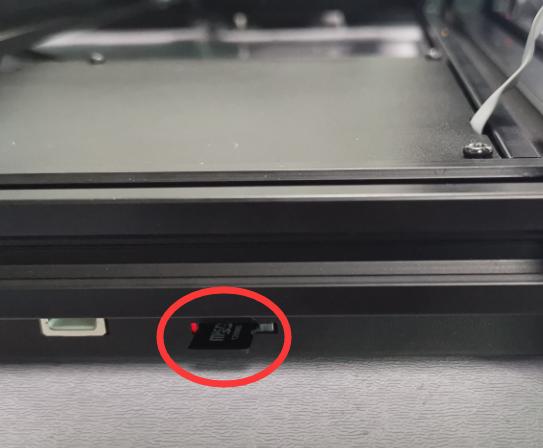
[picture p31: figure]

# More

## 1. About slicing:

The printer can only accept gcode file, if you want to print your own 3d model files, usually the file suffix are stl, AMF, Obj, etc. you need to convert it to a gcode file, this process is

## called slicing. About how to slicing a 3d model file, please refer to this guide

“Slicing guide for mixing color printer.pdf”.

## 2. About Bed auto leveling feature:

## Many factors will lead to the problem of uneven hot bed. This printer is equipped with a

Proximity sensor for automatic leveling of the hot bed. With this sensor, you can correct the

## unevenness of the hot bed. About more information, please refer to this guide:

“Auto leveling feaure user guide (PL-08N).pdf”.

## 3. About mixing color feature:

This machine is equipped with a mixing extruder, which can print single color, multi-color and gradient colors object. For the introduction of mixed color printing, please refer to this guide: “Operation guide for mixing color printer.pdf”.

## 4. About power loss recover feature:

## When you print from SD card, and power is lost when printing, the printer will resume to

Print from the last layer which printed before power lost automatically, about the detail, please refer to this guide: “Power loss recover feature.pdf”.

## NOTE: if you can’t find these guide in your SD card, please download from the

## below link:!

# https://github.com/ZONESTAR3D

## You can print something to upgrade your printer, we have made some printed part

and store the stl file to the SD card, you can feel free to slicing it and print it out, and then install them to your kit to make the printer is better.

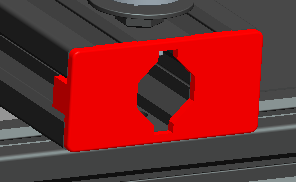
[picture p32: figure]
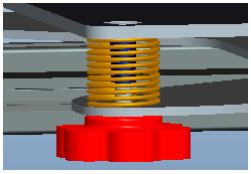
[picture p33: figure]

cap_af_20v.stl | cap_af_40v.stl | cap_m4nut.stl

## lcd12864_case_v2.stl

## You can add more functions in the machine by adding accessories, including:

## 32 bits control board (https://www.aliexpress.com/item/1005001300737027.html)

4.3" TFT (https://www.aliexpress.com/item/1005002378065646.html)- (https://www.aliexpress.com/item/1005002378065646.html)LCD screen (https://www.aliexpress.com/item/1005002378065646.html)

## Silent motor driver (https://www.aliexpress.com/item/4000596369015.html)

Filament run out (https://www.aliexpress.com/item/4001309957376.html) detector(FROD) (https://www.aliexpress.com/item/4001309957376.html)

## 3D Touch bed leveling sensor (https://www.aliexpress.com/item/1005001464420529.html)

## Magnetic flexible hot bed sticker (https://www.aliexpress.com/item/4000793898821.html)

## Hotbed glass (https://www.aliexpress.com/item/4001317243160.html)

## Hotbed Nuts (https://www.aliexpress.com/item/4000726717520.html)

## Z lead screw fix module (https://www.aliexpress.com/item/1005002401708373.html)

3 (https://www.aliexpress.com/item/1005001275429959.html)- (https://www.aliexpress.com/item/1005001275429959.html)IN (https://www.aliexpress.com/item/1005001275429959.html)- (https://www.aliexpress.com/item/1005001275429959.html)2 (https://www.aliexpress.com/item/1005001275429959.html)- (https://www.aliexpress.com/item/1005001275429959.html)OUT (https://www.aliexpress.com/item/1005001275429959.html) hotend

3 (https://www.aliexpress.com/item/1005001275429959.html)- (https://www.aliexpress.com/item/1005001275429959.html)IN (https://www.aliexpress.com/item/1005001275429959.html)- (https://www.aliexpress.com/item/1005001275429959.html)3 (https://www.aliexpress.com/item/1005001275429959.html)- (https://www.aliexpress.com/item/1005001275429959.html)OUT hotend (https://www.aliexpress.com/item/1005001275429959.html)

## Upgrade parts combine (https://www.aliexpress.com/item/1005002019863241.html)

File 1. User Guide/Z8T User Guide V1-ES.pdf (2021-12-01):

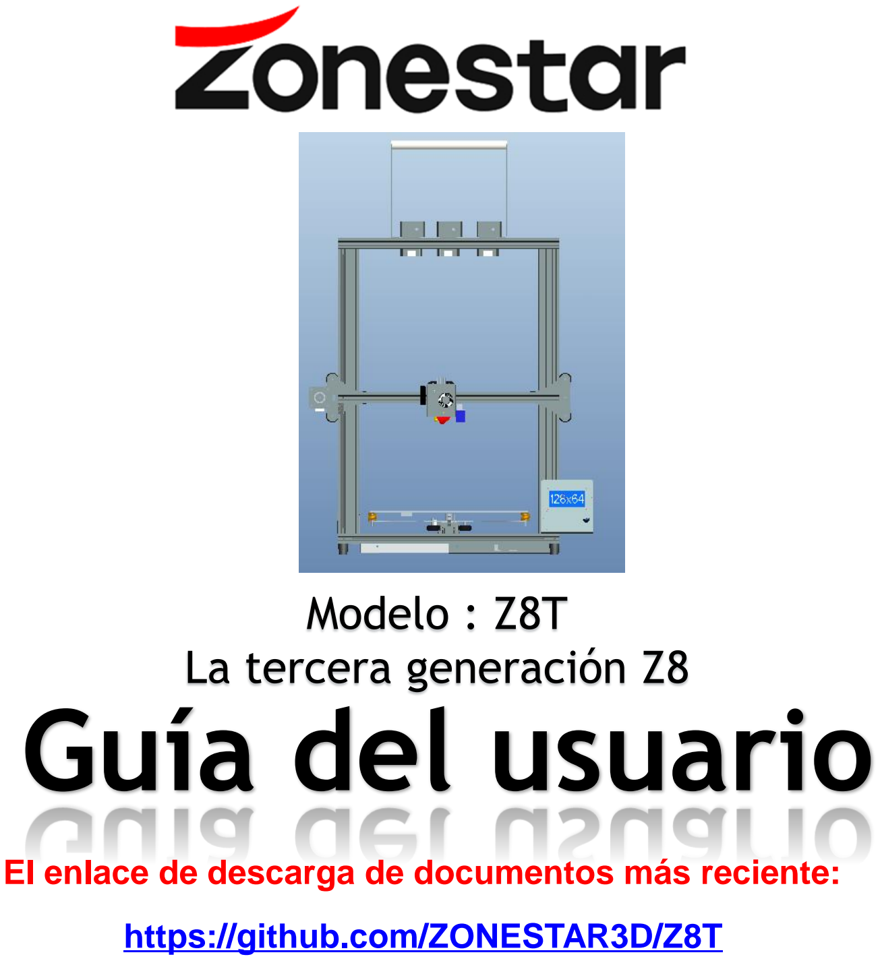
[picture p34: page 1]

## Modelo : Z8T La tercera generación Z8

# Guía del usuario

El enlace de descarga de documentos más reciente:

https://github.com/ZONESTAR3D/Z8T

## Lista de empaque

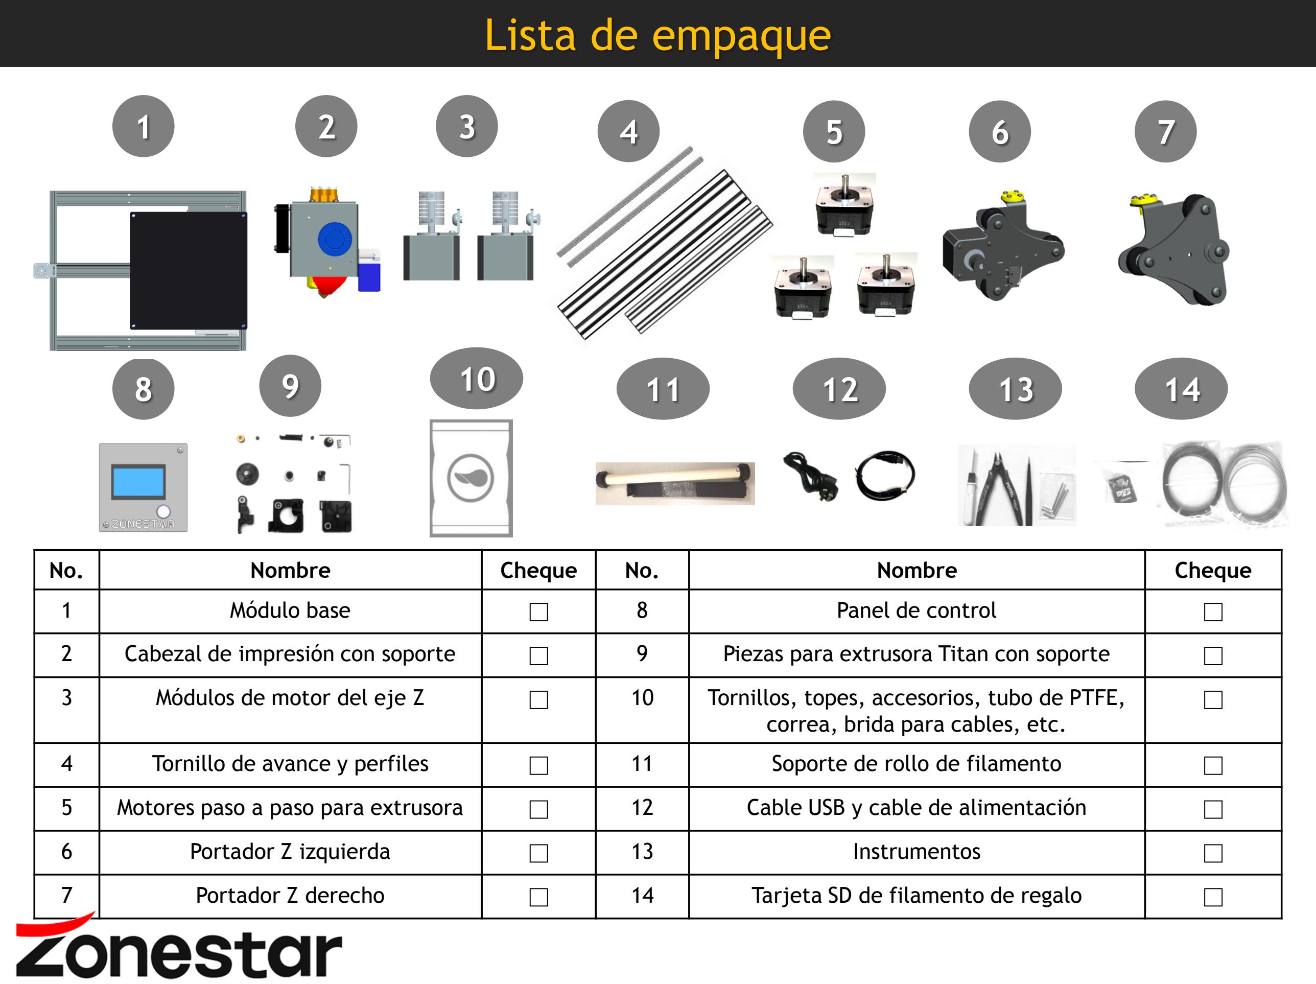
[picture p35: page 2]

No. | Nombre | Cheque | No. | Nombre | Cheque
1 | Módulo base | □ | 8 | Panel de control | □
2 | Cabezal de impresión con soporte | □ | 9 | Piezas para extrusora Titan con soporte | □
3 | Módulos de motor del eje Z | □ | 10 | Tornillos, topes, accesorios, tubo de PTFE, correa, brida para cables, etc. | □
4 | Tornillo de avance y perfiles | □ | 11 | Soporte de rollo de filamento | □
5 | Motores paso a paso para extrusora | □ | 12 | Cable USB y cable de alimentación | □
6 | Portador Z izquierda | □ | 13 | Instrumentos | □
7 | Portador Z derecho | □ | 14 | Tarjeta SD de filamento de regalo | □

8 14

1 | 2 | 3 | 4 | 5 | 6 | 7
9 | 11 | 12 | 13 10

## Montar el extrusor Titan (3 juegos)

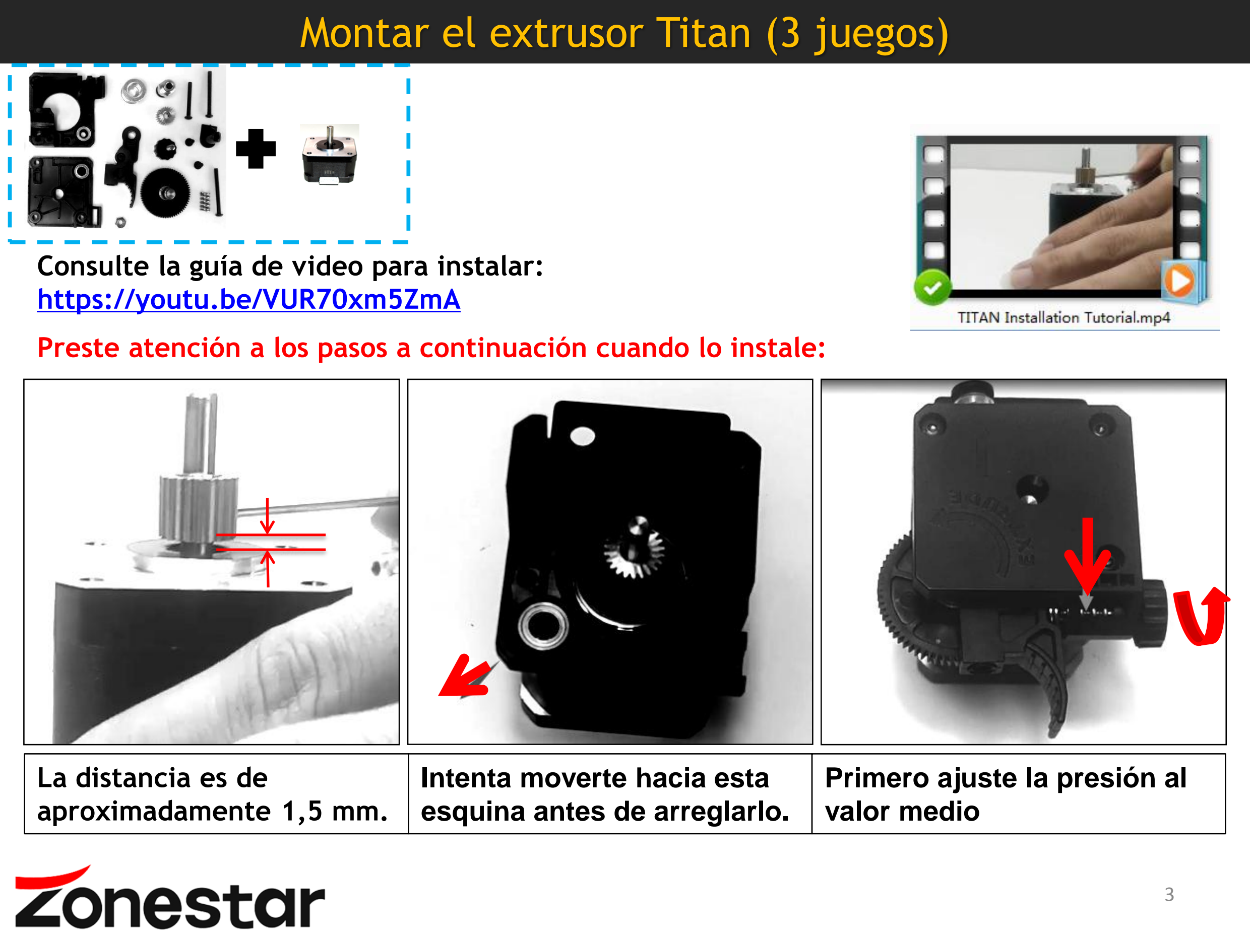
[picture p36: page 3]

Consulte la guía de video para instalar: https://youtu.be/VUR70xm5ZmA

Preste atención a los pasos a continuación cuando lo instale:

Intenta moverte hacia esta esquina antes de arreglarlo.

La distancia es de
aproximadamente 1,5 mm.

Primero ajuste la presión al valor medio

## Instalar piezas del eje Z

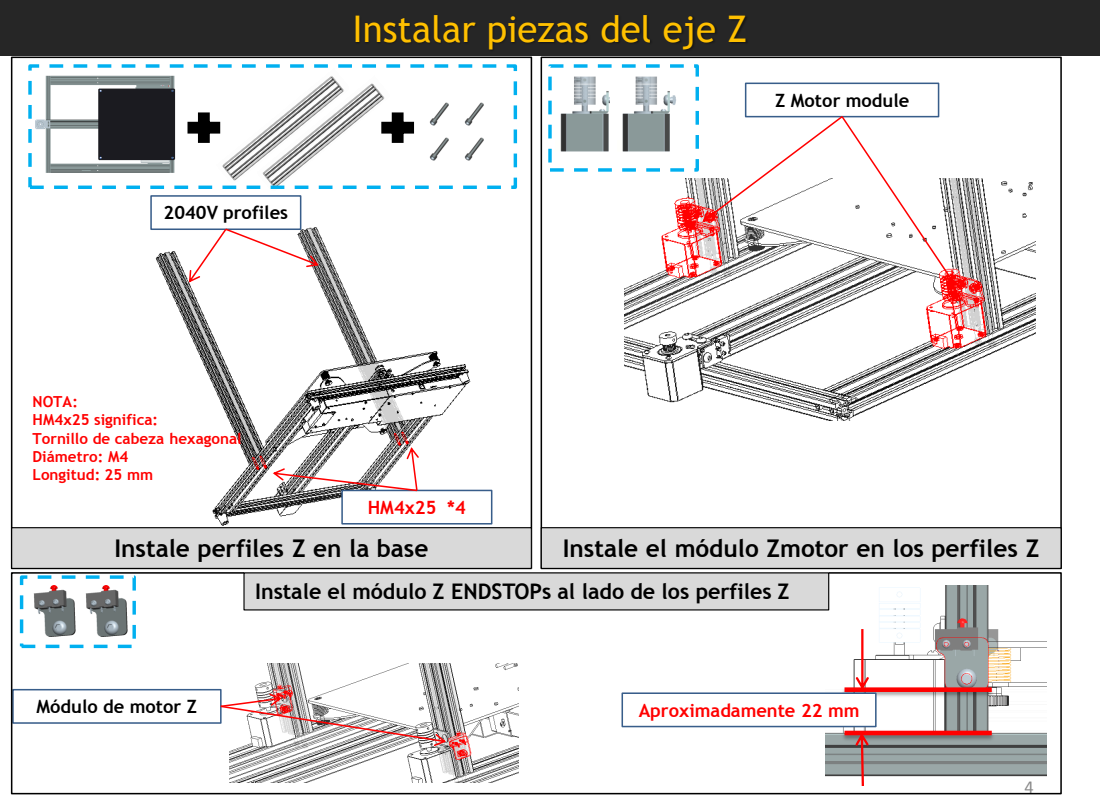
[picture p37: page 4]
2040V profiles; Z Motor module; Aproximadamente 22 mm

NOTA:
HM4x25 significa:
Tornillo de cabeza hexagonal
Diámetro: M4
Longitud: 25 mm

Instale perfiles Z en la base

Instale el módulo Zmotor en los perfiles Z

Instale el módulo Z ENDSTOPs al lado de los perfiles Z

Módulo de motor Z

## Instalar piezas del eje Z

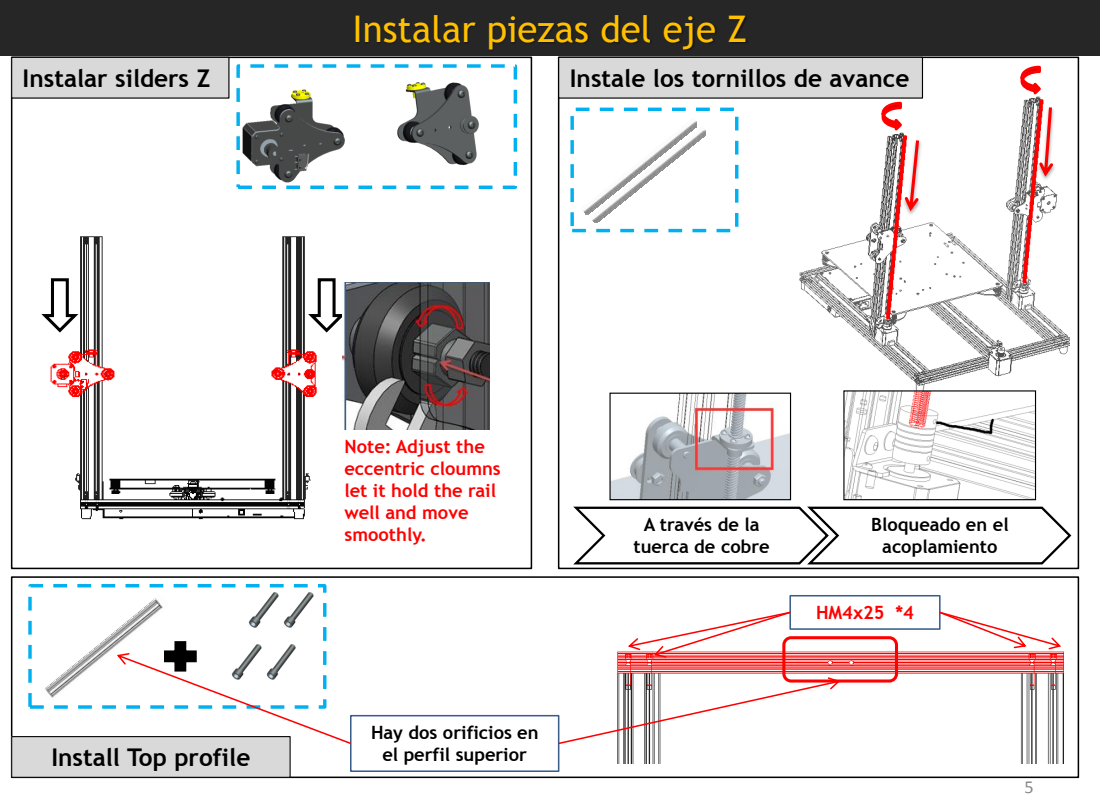
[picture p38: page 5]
Instalar silders Z; Instale los tornillos de avance

Note: Adjust the
eccentric cloumns
let it hold the rail
well and move
smoothly.

A través de la
tuerca de cobre

Bloqueado en el
acoplamiento

Hay dos orificios en
el perfil superior

Install Top profile

## Instalar piezas del eje X

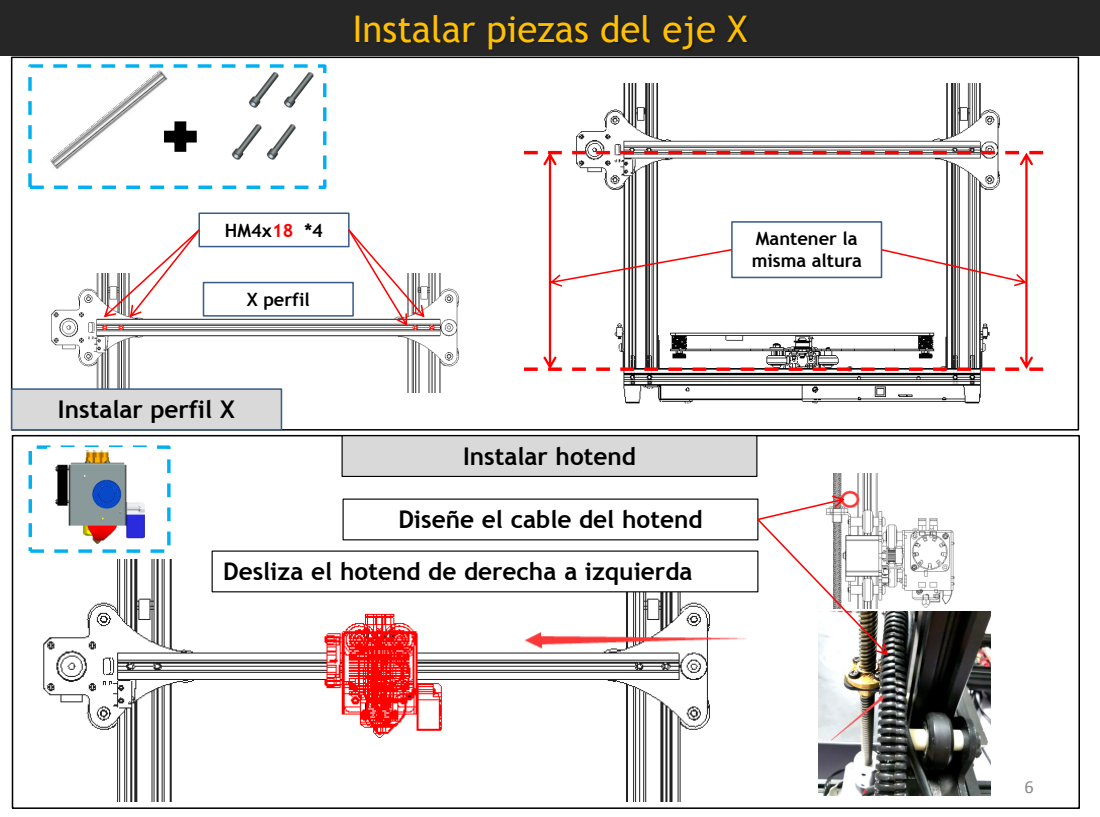
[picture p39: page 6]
X perfil; Mantener la misma altura; Instalar perfil X; Instalar hotend

Diseñe el cable del hotend

Desliza el hotend de derecha a izquierda

## Instale la correa X

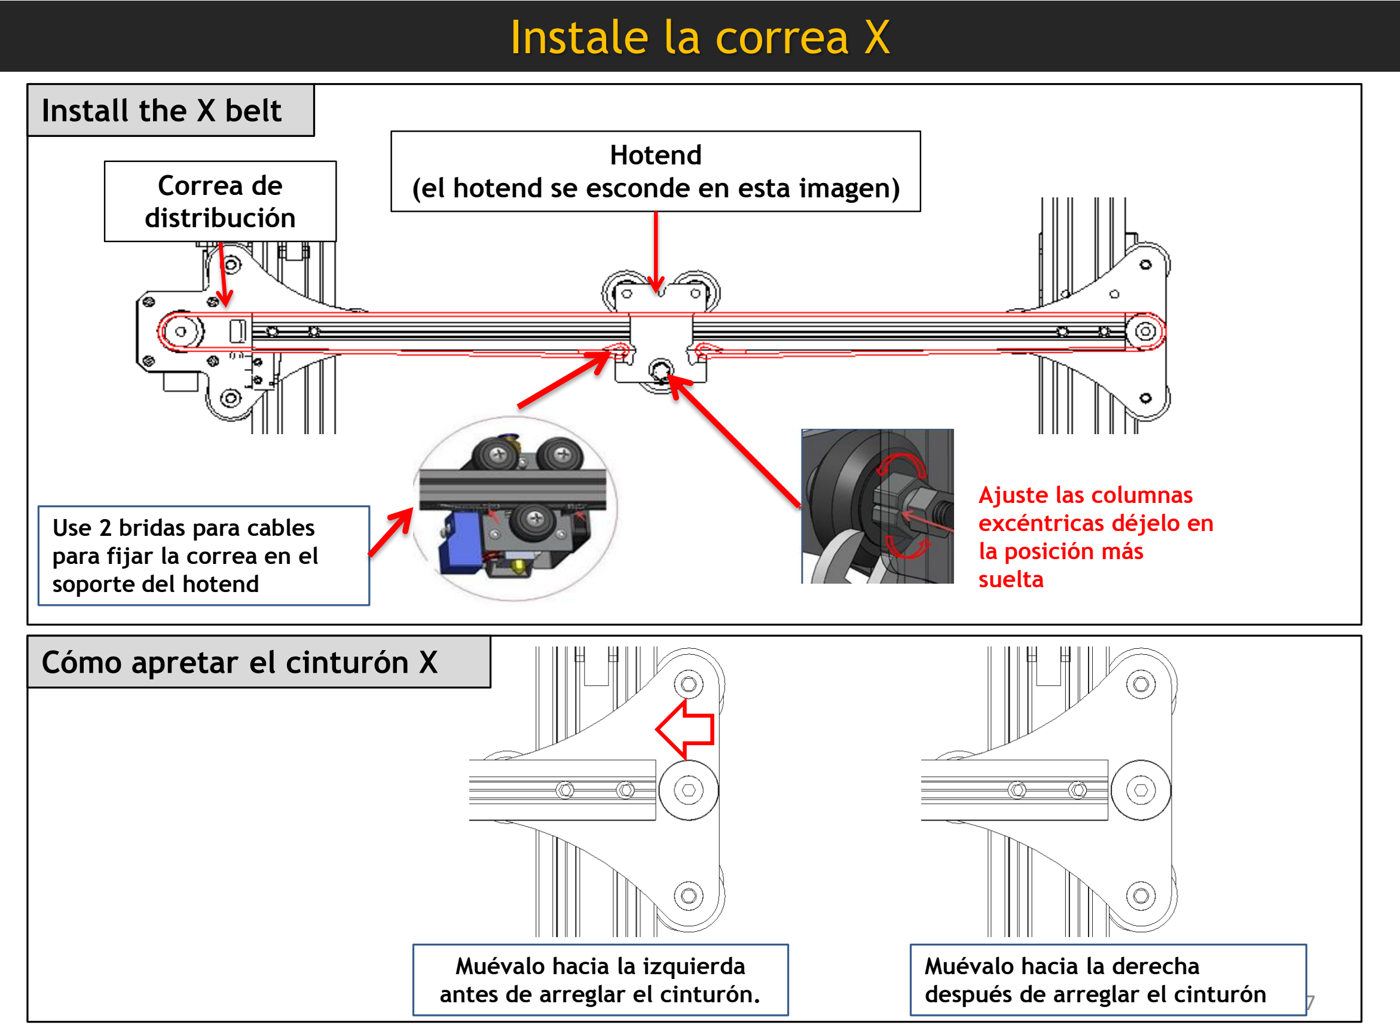
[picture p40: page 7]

Install the X belt

Correa de
distribución

Hotend
(el hotend se esconde en esta imagen)

Ajuste las columnas
excéntricas déjelo en
la posición más
suelta

Use 2 bridas para cables
para fijar la correa en el soporte del hotend

Muévalo hacia la izquierda antes de arreglar el cinturón.

Muévalo hacia la derecha
después de arreglar el cinturón

Cómo apretar el cinturón X

## Instale las otras partes

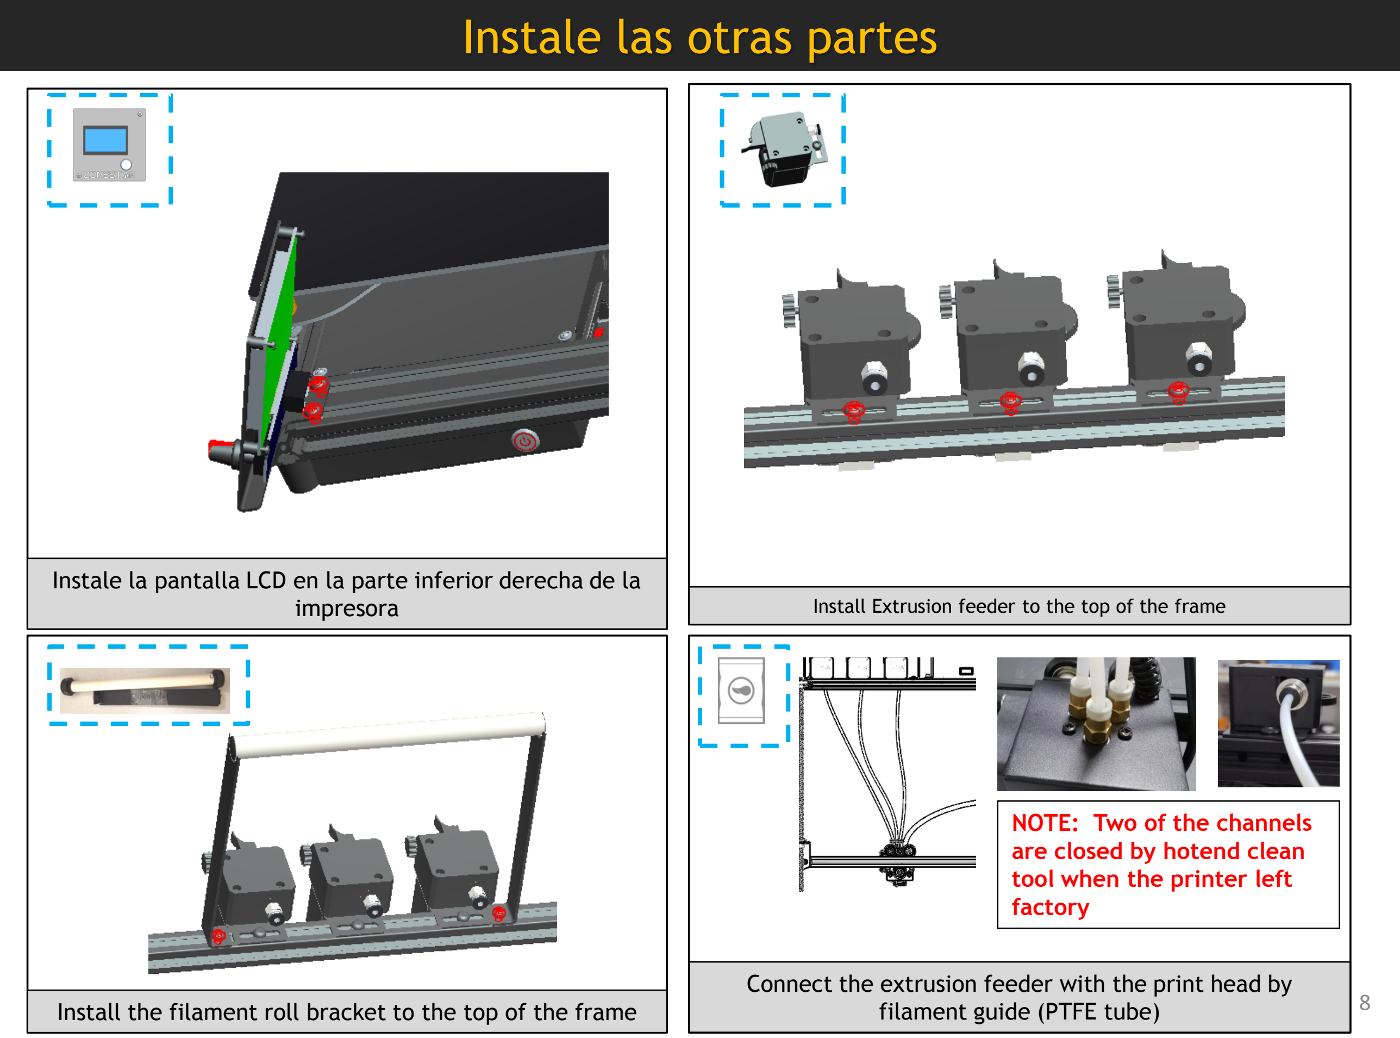
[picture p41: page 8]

Instale la pantalla LCD en la parte inferior derecha de la
impresora | Install Extrusion feeder to the top of the frame

Install the filament roll bracket to the top of the frame

NOTE: Two of the channels
are closed by hotend clean tool when the printer left factory

Connect the extrusion feeder with the print head by filament guide (PTFE tube)

## Ajustar la altura de Z ENDSTOP

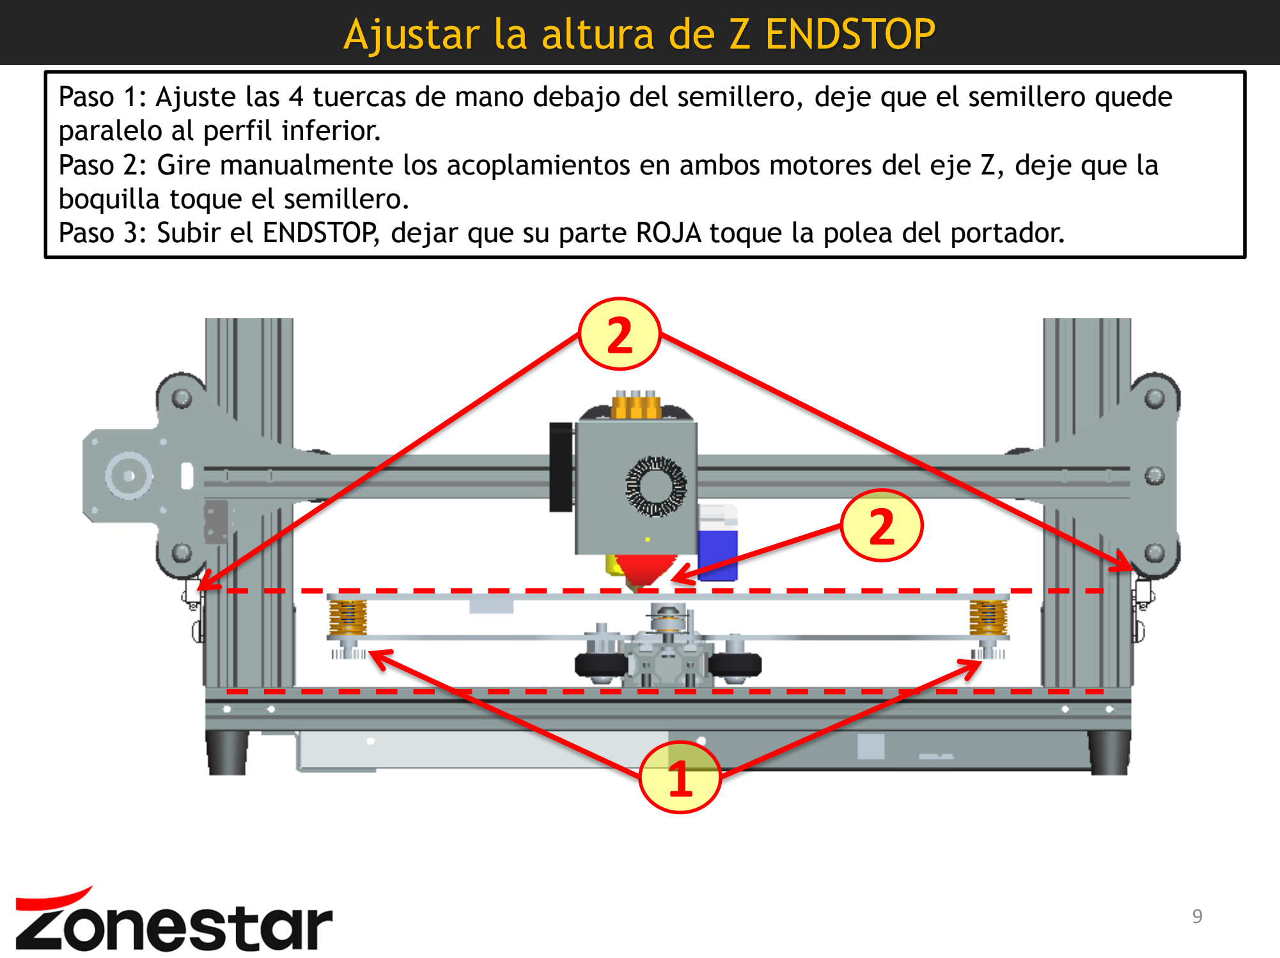
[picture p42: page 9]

Paso 1: Ajuste las 4 tuercas de mano debajo del semillero, deje que el semillero quede paralelo al perfil inferior.
Paso 2: Gire manualmente los acoplamientos en ambos motores del eje Z, deje que la boquilla toque el semillero.
Paso 3: Subir el ENDSTOP, dejar que su parte ROJA toque la polea del portador.

1

2

2

# !! ATENCIÓ N!!

¡Tenga cuidado durante la instalación para evitar riesgos de descargas eléctricas!

¡Verifique el cableado! ¡UN CABLEADO INCORRECTO PUEDE DAÑ AR EL DISPOSITIVO ELECTRÓ NICO!

Coloque el interruptor 110V / 220V (en el lateral de la fuente de alimentación) en la posición correcta de acuerdo con el voltaje de energía de su ciudad.

Coloque el cable del motor en las ranuras del perfil y cúbralas con una cubierta de perfil de plástico y use una brida para envolver los cables libres.

Deje de trabajar inmediatamente si el motor tiene vibraciones o ruidos anormales; de lo contrario, los módulos del controlador pueden dañarse.
Asegúrese de que el ventilador de enfriamiento del hotend esté funcionando cuando la temperatura de la boquilla sea superior a 60 grados; de lo contrario, verifique el cableado nuevamente.

DC-IN, HOTBED tiene una corriente de funcionamiento mayor, asegúrese de que estos cables hagan contacto bien con el terminal.

Paso 4: Mueva manualmente el hotend y el semillero para ver si el movimiento es suave, de lo contrario, ajuste la tuerca excéntrica hasta que el motor se mueva suavemente. Consulte el procedimiento de instalación.

Paso 3: Mueva el hotend y el semillero a sus respectivas posiciones del interruptor de límite para verificar si el contacto es bueno y hay un sonido claro. De lo contrario, compruebe el interruptor de límite y vuelva a montarlo.

Paso 7: Gire manualmente la varilla roscada del eje z para verificar si el interruptor de límite del eje z entra en contacto de manera confiable.

Paso 5: Verifique si la correa de transmisión de los ejes X e Y está firmemente instalada. Si está demasiado flojo, intente apretarlo.

Es muy importante comprobar la máquina antes de encenderla. ¡Puede eliminar los problemas ocasionados por algunos hardware para garantizar una impresión fluida!

Paso 6: Verifique si la varilla del tornillo está ensamblada en su lugar y si el tornillo está apretado

Paso 1: compruebe si la polea de sincronización del eje X&Y está fijada en el eje del motor y los acoplamientos están fijados en el eje de los motores Z.

Paso 2: compruebe si los tornillos de avance se han fijado en el eje del acoplamiento.

## Acerca de las piezas de electrónica

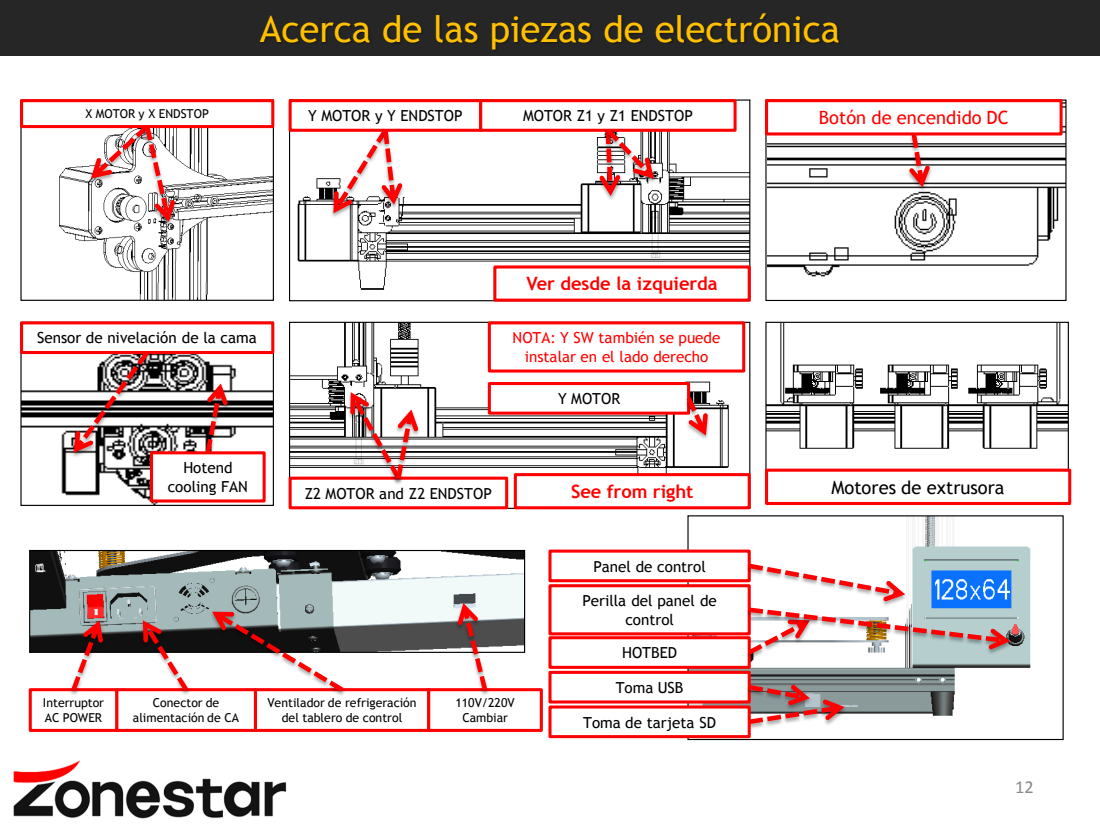
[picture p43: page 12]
X MOTOR y X ENDSTOP; Y MOTOR y Y ENDSTOP; MOTOR Z1 y Z1 ENDSTOP; Hotend; cooling FAN; Z2 MOTOR and Z2 ENDSTOP; Y MOTOR; Interruptor AC POWER; 110V/220V Cambiar

Botón de encendido DC

Ver desde la izquierda

Sensor de nivelación de la cama

NOTA: Y SW también se puede
instalar en el lado derecho

Motores de extrusora

See from right

Panel de control

Perilla del panel de control

HOTBED

Toma USB

Conector de
alimentación de CA

Ventilador de refrigeración
del tablero de control

Toma de tarjeta SD

## Fotos de cableado

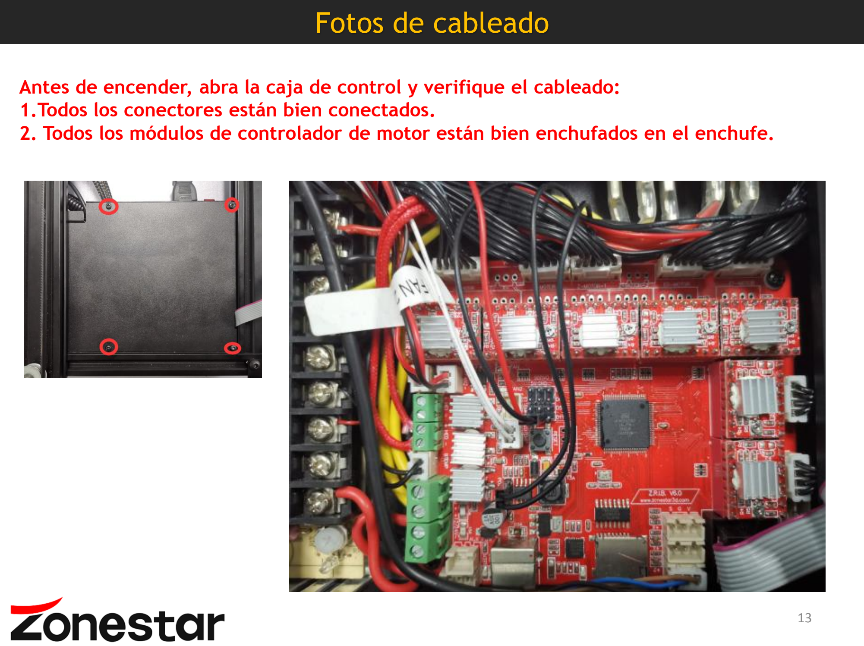
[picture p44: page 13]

Antes de encender, abra la caja de control y verifique el cableado:
1.Todos los conectores están bien conectados.
2. Todos los módulos de controlador de motor están bien enchufados en el enchufe.

## Diagrama de cableado

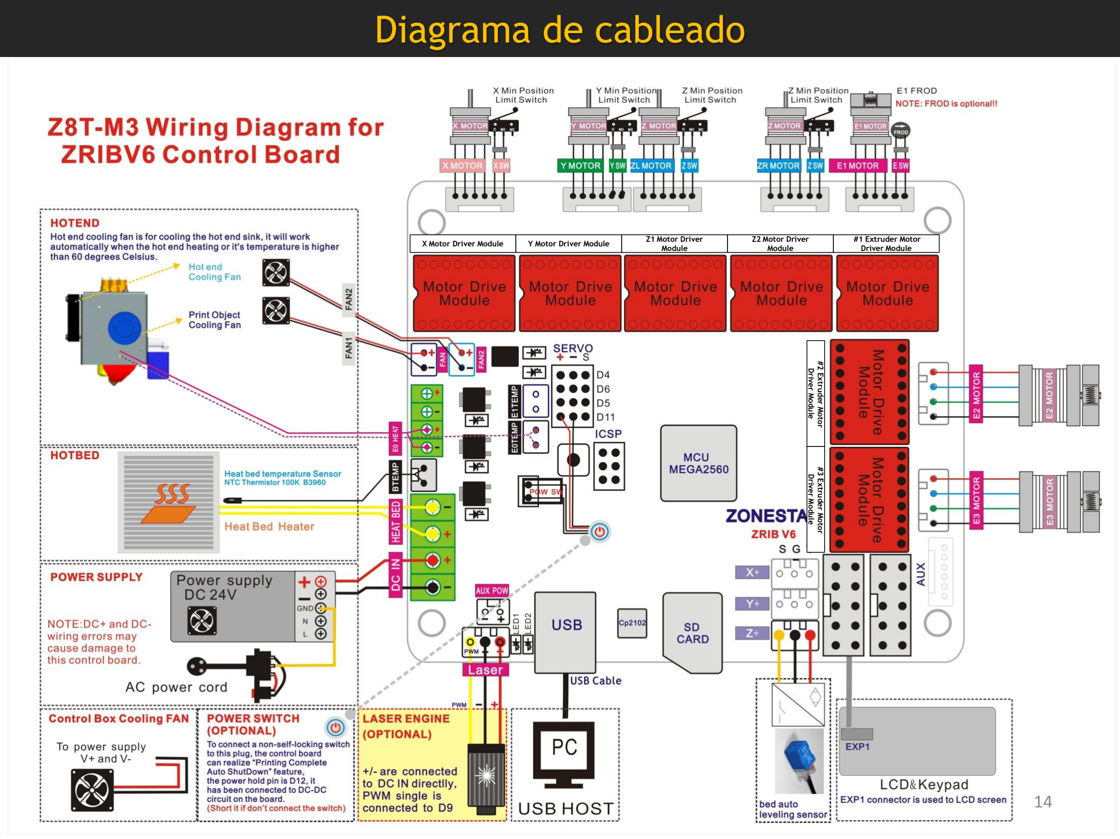
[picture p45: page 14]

X Motor Driver Module | Y Motor Driver Module | Z1 Motor Driver Module

Z2 Motor Driver
Module

#1 Extruder Motor

Driver Module

#2 Extruder Motor

Driver Module

#3 Extruder Motor

Driver Module

## Distribuya los alambres / cables

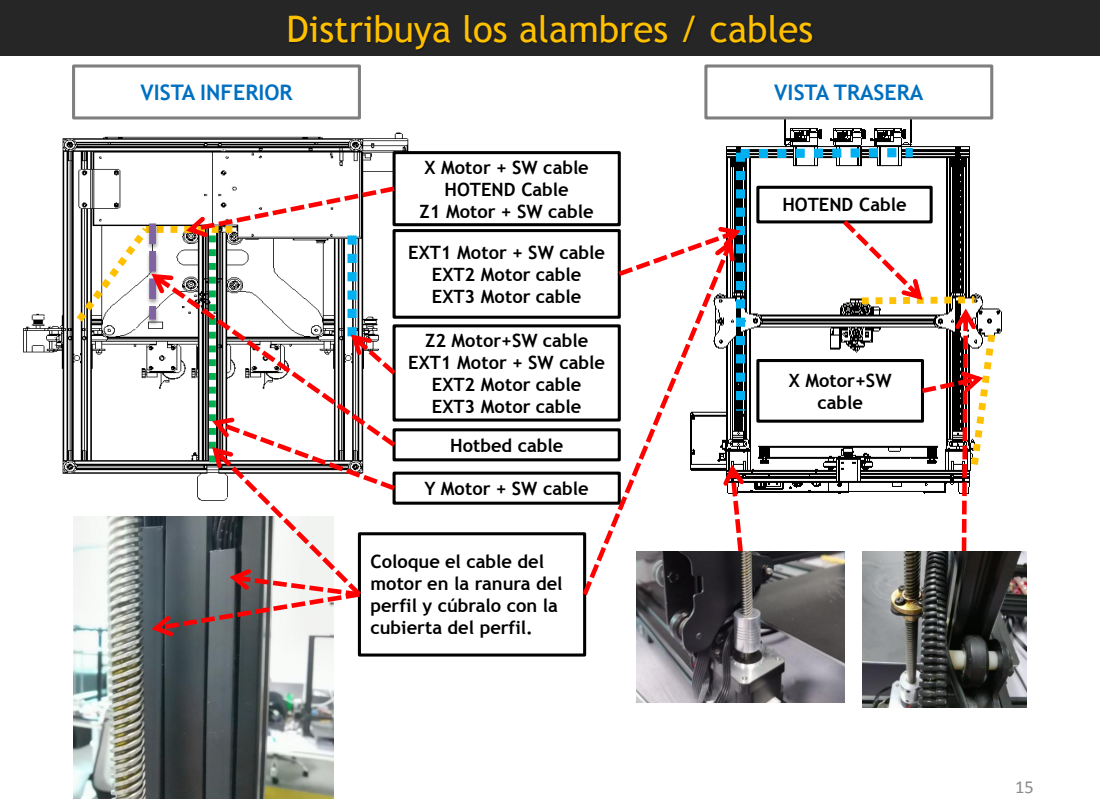
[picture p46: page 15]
Hotbed cable; VISTA INFERIOR; VISTA TRASERA; HOTEND Cable; X Motor+SW cable

X Motor + SW cable
HOTEND Cable
Z1 Motor + SW cable

EXT1 Motor + SW cable
EXT2 Motor cable
EXT3 Motor cable

Z2 Motor+SW cable

Y Motor + SW cable

Coloque el cable del
motor en la ranura del
perfil y cúbralo con la
cubierta del perfil.

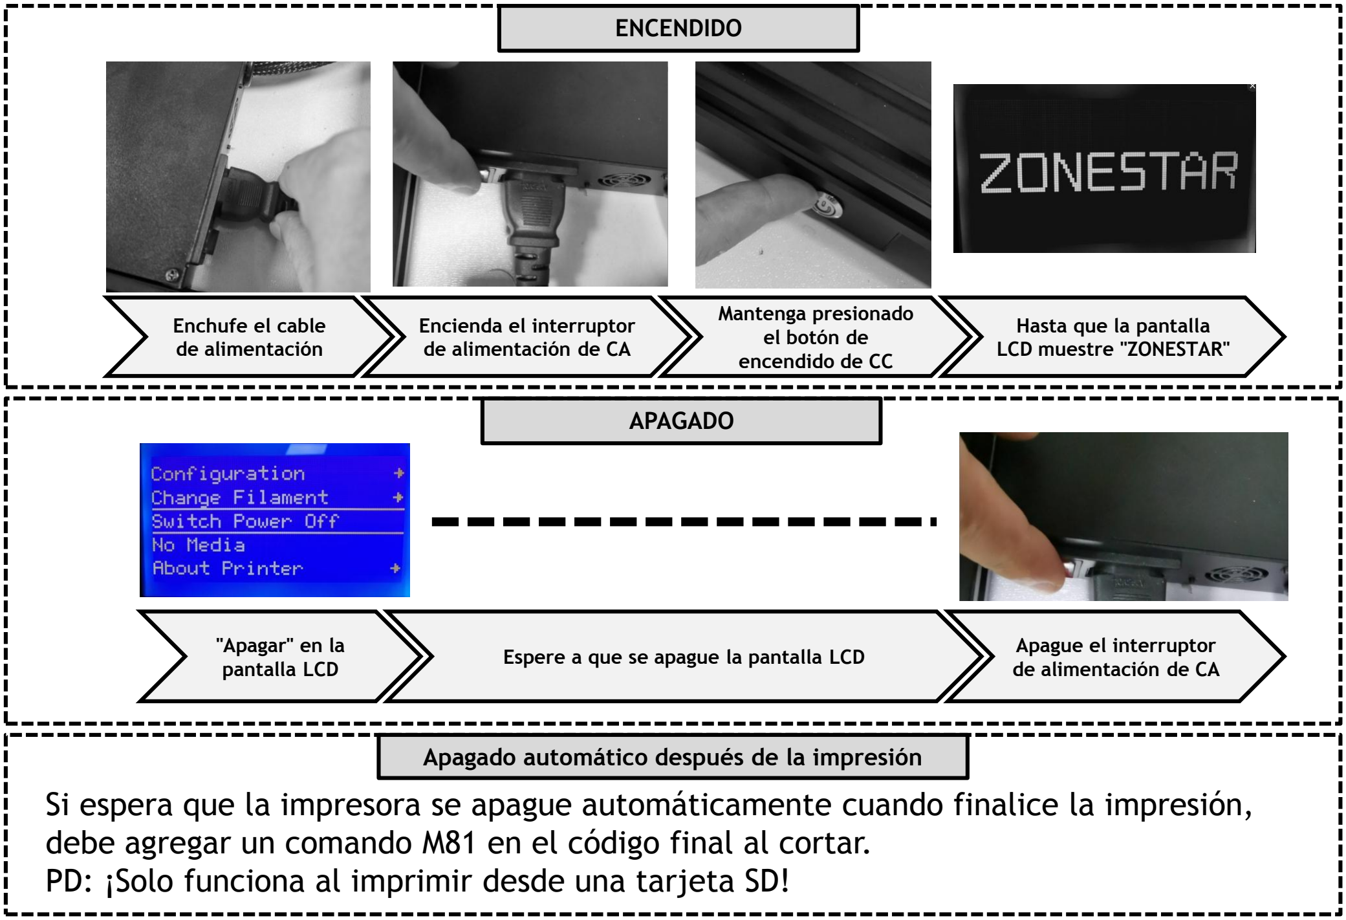
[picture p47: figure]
Espere a que se apague la pantalla LCD; APAGADO; "Apagar" en la pantalla LCD; Apague el interruptor de alimentación de CA; Enchufe el cable de alimentación; Encienda el interruptor de alimentación de CA; Mantenga presionado el botón de encendido de CC; Hasta que la pantalla LCD muestre "ZONESTAR"; ENCENDIDO

Apagado automático después de la impresión
Si espera que la impresora se apague automáticamente cuando finalice la impresión, debe agregar un comando M81 en el código final al cortar.
PD: ¡Solo funciona al imprimir desde una tarjeta SD!

## Menú y funcionamiento de la pantalla LCD

Operación de la perilla: <Rotación en el sentido de las agujas del reloj>: Siguiente elemento / Valor +. <Rotación en sentido antihorario>: artículo / valor anterior -. <Pulsar>: Entrar / Ejecutar.

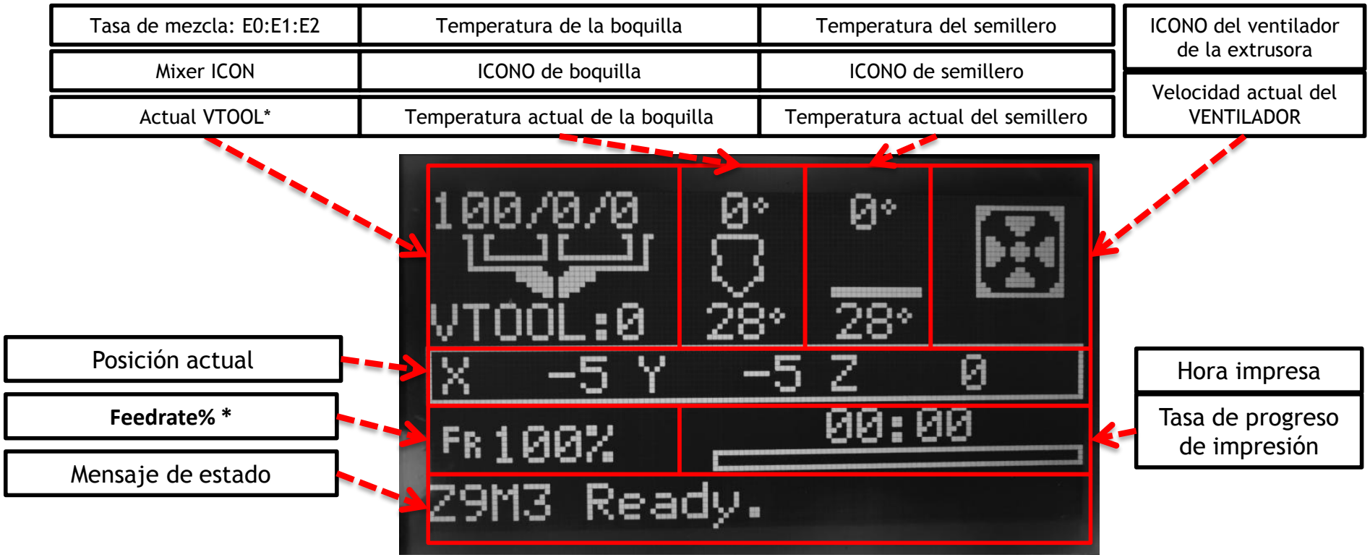
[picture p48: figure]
Mensaje de estado; Hora impresa; Tasa de progreso de impresión; ICONO del ventilador de la extrusora; Posición actual; Feedrate% *; Actual VTOOL*; Tasa de mezcla: E0:E1:E2; Mixer ICON; Temperatura de la boquilla; ICONO de boquilla; Temperatura actual de la boquilla; Temperatura del semillero; ICONO de semillero; Temperatura actual del semillero; Velocidad actual del VENTILADOR

Para obtener más información sobre el menú de la pantalla LCD, consulte"LCD12864 Menu Description.pdf".

VTOOL: En una impresora de color único o multicolor en general, cada motor de extrusión corresponde a una boquilla, luego una extrusora + una boquilla constituye una cadena de herramientas; En la extrusora de mezcla de colores, varios motores de extrusión corresponden a una boquilla. El establecimiento de diferentes relaciones de rotación de los motores de extrusión puede formar múltiples cadenas de herramientas virtuales. El hotend M3 tiene hasta 16 VTOOLs. Acerca de los detalles, consulte “Mixing Color Hotend User Guide.pdf” Feedrate: Al imprimir desde una tarjeta SD, ajustar la velocidad de alimentación puede ajustar la velocidad
de impresión, se basa en la velocidad establecida por el archivo gcode al cortar. | 17


Quitar el papel | Pegar en el semillero

NOTA :

Tenga cuidado al pegar, evite la influencia de las burbujas de aire porque la cama caliente no es lisa.
Consejos :

Primero arranca un lado de la pegatina en la parte posterior, luego nivela con una pala de un lado al otro lado y luego, gradualmente, quita la pegatina en la parte posterior.

Después de terminar de ensamblar y cablear, siga los pasos a continuación para verificar.
Paso 1: Antes de encender la alimentación, confirme nuevamente:
✓ | Compruebe si se ha configurado correctamente en el interruptor de selección de voltaje de alimentación de 110 V / 220 V.
✓ | Compruebe si los componentes están conectados correctamente. Especialmente, DC + y DC- de la alimentación de DC no se
| invirtieron, el cableado está en buen contacto con los terminales y no hay cables en cortocircuito.
✓ | Compruebe si el cable de la pantalla LCD está bien conectado al conector EXP1 en la placa de control.
Paso 2: Verifique el sensor de temperatura:

Enchufe el cable de alimentación de CA y encienda la alimentación de CA, mire la pantalla LCD, la temperatura debe ser casi la misma que la temperatura ambiente.
Paso 3: Compruebe los motores de los ejes X, Y y Z y ENDSTOPS:

DO: Motion>>Move axis>>Move X/Y/Z>> Move 10mm. Haga clic y gire la perilla para mover el eje X/Y/Z.

CHECK: Compruebe si el semillero puede moverse hacia la izquierda/derecha(X), adelante/atrás (Y), o si el semillero puede moverse hacia arriba
| / abajo (Z). NOTA: Si la X y la Y no se pueden mover correctamente, p. Ej. al mover X o Y, el cabezal de impresión se mueve en 45 grados, significa que el motor x o el motor Y no funcionan, verifique el cableado.

CHECK: Mantenga presionado el interruptor de límite X/Y e intente reducir el valor de Move X/Y, el cabezal de impresión debe dejar de
| moverse; de lo contrario, verifique la conexión del interruptor de límite X/Y.

CHECK: Mantenga presionado el interruptor de límite Z e intente reducir el valor de Move Z, el semillero debe dejar de moverse; de lo
| contrario, verifique la conexión del interruptor de límite Z.

Paso 4: Revise calentadores y ventiladores:

1. Temperature>>Nozzle: 180, establezca la temperatura de la boquilla en 180 grados y luego regrese al menú de información, la temperatura de la boquilla aumentará, por lo general es de un grado por segundo más o menos.
2. Temperature>>Bed: 60, establezca la temperatura de la cama de calor en 60 grados, y luego regrese al menú de información, la temperatura de la cama caliente aumentará, por lo general es de un grado cada 2 segundos más o menos.
3. Verifique el ventilador de enfriamiento HOTEND. Cuando la temperatura de la boquilla es superior a 60 grados, el ventilador de enfriamiento en el lateral del cabezal de impresión debería funcionar.

4 . Compruebe el ventilador del extrusor, Temperature>>Fan Speed: 100%, el ventilador de la extrusora debería funcionar.

Extruder fan work; HOTEND cooling fan work When nozzle temperature over 60 degree

Paso 5: Verifique los alimentadores de extrusión:

1. Temperature>>Nozzle: 180, set the nozzle temperature to 180 degrees, and then return to info menu, waiting for the temperature reached to the setting.

### 2. Establezca la proporción de mezcla de todas las extrusoras en el mismo (33:33:34):

Mixer>>Set Mix>>Active V-tool: 0>> set to Active V-tool: 3
3. Move Axis>>Extruder>>Move 10mm>>Extruder: +20mm, observe el engranaje del alimentador de extrusión y verifique si todos los alimentadores de extrusión funcionarán.

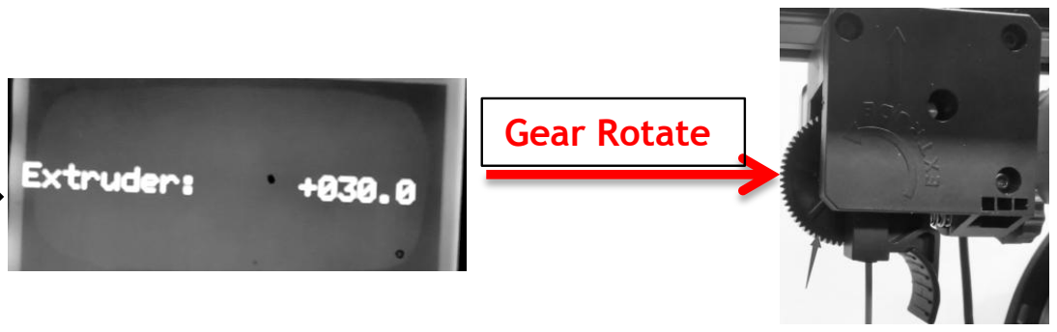
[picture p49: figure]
Gear Rotate

## Resolución de problemas rápidamente

La pantalla LCD no se muestra después de encender | 1. La luz de fondo de la pantalla LCD no se enciende. Posibles motivos: el cable de alimentación de CA no está enchufado; DC + y - están invertidos; las tomas de corriente están desconectadas con la fuente de alimentación. 2. La luz de fondo de la luz LCD pero no tiene caracteres. Posibles razones: el cable LCD está invertido; error de firmware o perdido;

Temperatura de error

El motor o el alimentador de extrusión no funcionan correctamente | 1. La fuente de alimentación no funciona (Nota: USB también puede suministrar energía de + 5V y dejar que la pantalla LCD se muestre, pero no puede suministrar energía a los motores y al calentador). 2. El cable del motor está desconectado. 3. El módulo de accionamiento del motor no se conectó bien con el zócalo de la placa de control. 4. Calentar la boquilla a más de 150 grados antes de la extrusión.
Error de dirección del motor | 1. El motor no está conectado al conector correcto de la placa de control, como los enchufes X e Y intercambiados. 2. La secuencia de cables del cable del motor es incorrecta. 3. La versión de firmware es incorrecta.
Emisión del interruptor de límite (ENDSTOP) | 1. El cable del interruptor de límite está desconectado del tablero de control. 2. El interruptor de límite está conectado al conector incorrecto, por ejemplo, intercambió los interruptores de límite X e Y. 3. El cable está desconectado con el interruptor de límite. 4. Verifique la única del interruptor de límite, debe estar conectado al pin “S” y “GND” del conector en el tablero de control.

El sensor de temperatura
Hotend no se conecta bien

El sensor de temperatura de la cama caliente no se conecta bien

1. La impresora se reinicia automáticamente al calentar la cama de calor o la boquilla. Compruebe si el interruptor de selección de voltaje de la fuente de alimentación de CA está configurado correctamente y si el cable de alimentación de CC está bien conectado.
2. No se puede llegar a Hotend a la temperatura de ajuste. Compruebe si falta el termistor en el bloque calentado. Compruebe si el cable del calentador del cabezal de impresión está bien conectado.
3. No se puede llegar a la cama caliente a la temperatura establecida. A) Compruebe si el cableado está bien conectado. B) Compruebe si la temperatura ambiente es inferior a 5 grados.

Problema de la
cama de calor y el
hotend

## Prepárese para imprimir: nivele el semillero

asegúrese de que no haya ningún filamento en el extremo de la boquilla, si no, retírelo con unos alicates diagonales. 1

2

3

Hacer Motion>> Auto Home, Espere que el hotend vuelva a la posición original.

Mire la boquilla y asegúrese de que la boquilla esté más alta que la cama; de lo contrario, apriete las tuercas de mano debajo de la cama para bajar el semillero o afloje estas tuercas para subir la cama.

4

Hacer Motion>> Level Corners, la boquilla irá a las esquinas, ajuste las tuercas de mano debajo del semillero, deje que la boquilla casi toque el semillero. Para conseguir una distancia adecuada, puedes poner un papel A4 en el semillero, y cuando la distancia entre la boquilla y el semillero solo pueda insertar un papel, será perfecto.

Hacer “next corner”, y vuelva a ajustar. Repita este paso una y otra vez, hasta que las cuatro esquinas estén a la misma altura.. 5


## Prepárese para imprimir - Cargar filamento

Boquilla de precalentamiento : Temperature>> Nozzle, ajústelo a aproximadamente 180 grados (para PLA) o 220 grados (para filamentos de ABS y PETG), luego la boquilla se calentará. Esperando temperatura de la boquilla alcanzada al ajuste.

1

2

Presione el asa en el alimentador de extrusión e inserte el filamento, hasta que el filamento entre en el hotend.
Hacer “Motion>> Move axis>>Extruder>>Move 1mm>>extruder: 30mm”, luego, en el sentido de las agujas del reloj, gire la perilla lentamente, hasta que pueda ver que el filamento fluye desde la boquilla.

3


que el filamento salga Precalentar la boquilla

NOTA: Recomendamos encarecidamente que comience con un solo color. Cuando el producto sale de fábrica, hemos cerrado dos canales con "hotend clean tool". ¡Puedes utilizar el canal que no está cerrado para imprimir tus primeros trabajos!

# Imprima un objeto 3D de prueba desde la tarjeta SD

1

Inserte la tarjeta SD en la ranura para tarjetas SD en la caja de control y luego encienda la máquina.

2

Hacer “Print from Media >> Test_gcode\Single Color\xyz_cube.gcode”, presione la perilla para comenzar a imprimir.

3

Espere a que la impresora termine de calentarse y comience a imprimir, observe la distancia desde la boquilla hasta la cama, haga doble clic en la perilla del menú LCD y configure el desplazamiento z si la distancia no es perfecta, deje que el filamento se adhiera bien al semillero.


## Más

### 1. Sobre rebanar:

La impresora solo puede aceptar archivos gcode, si desea imprimir sus propios archivos de modelo 3D, generalmente el sufijo del archivo es stl, AMF, Obj, etc.Necesita convertirlo en un archivo gcode, este proceso se llama corte. Acerca de cómo cortar un archivo de modelo 3D, consulte esta guía “Slicing guide for mixing color printer.pdf”.

### 2. Nivelación automática de la cama :

Muchos factores conducirán al problema de la cama caliente desigual. Esta impresora está equipada con un sensor de proximidad para la nivelación automática de la cama caliente. Con este sensor, puede corregir las irregularidades de la cama caliente. Para obtener más información, consulte esta guía: “Auto leveling feaure user guide (PL-08N).pdf”.

### 3. Mezcla de color :

Esta máquina está equipada con una extrusora mezcladora, que puede imprimir objetos de un solo color, multicolor y colores degradados. Para la introducción de la impresión de colores mezclados, consulte este guía:“Operation guide for mixing color extruder.pdf”.

### 4. Recuperación de pérdida de energía:

Cuando imprime desde la tarjeta SD y se pierde energía al imprimir, la impresora reanudará la impresión desde la última capa que se imprimió antes de que se perdiera la energía automáticamente, sobre los detalles, consulte esta guía: “Power loss recover feature.pdf”.
NOTE: if you can’t find these guide in your SD card, please download from the below link: https://github.com/ZONESTAR3D/Z8T

Puede imprimir algo para actualizar su impresora, hemos hecho una parte impresa y almacenamos el archivo stl en la tarjeta SD, puede cortarlo e imprimirlo, y luego instalarlos en su kit para que la impresora sea mejor .


cap_af_20v.stl | cap_af_40v.stl | cap_m4nut.stl


lcd12864_case_v2.stl

Puede agregar más funciones en la máquina agregando accesorios, que incluyen:

•32 bits control board (https://www.aliexpress.com/item/1005001300737027.html)

•4.3" TFT (https://www.aliexpress.com/item/1005002378065646.html)- (https://www.aliexpress.com/item/1005002378065646.html)LCD screen (https://www.aliexpress.com/item/1005002378065646.html)

•Silent motor driver (https://www.aliexpress.com/item/4000596369015.html)

•Filament run out (https://www.aliexpress.com/item/4001309957376.html) detector(FROD) (https://www.aliexpress.com/item/4001309957376.html)

•3D Touch bed leveling sensor (https://www.aliexpress.com/item/1005001464420529.html)

•Magnetic flexible hot bed sticker (https://www.aliexpress.com/item/4000793898821.html)

•Hotbed glass (https://www.aliexpress.com/item/4001317243160.html)

•Hotbed Nuts (https://www.aliexpress.com/item/4000726717520.html)

•Z lead screw fix module (https://www.aliexpress.com/item/1005002401708373.html)

•3 (https://www.aliexpress.com/item/1005001275429959.html)- (https://www.aliexpress.com/item/1005001275429959.html)IN (https://www.aliexpress.com/item/1005001275429959.html)- (https://www.aliexpress.com/item/1005001275429959.html)2 (https://www.aliexpress.com/item/1005001275429959.html)- (https://www.aliexpress.com/item/1005001275429959.html)OUT (https://www.aliexpress.com/item/1005001275429959.html) hotend (https://www.aliexpress.com/item/1005001275429959.html)

•3 (https://www.aliexpress.com/item/1005001275429959.html)- (https://www.aliexpress.com/item/1005001275429959.html)IN (https://www.aliexpress.com/item/1005001275429959.html)- (https://www.aliexpress.com/item/1005001275429959.html)3 (https://www.aliexpress.com/item/1005001275429959.html)- (https://www.aliexpress.com/item/1005001275429959.html)OUT hotend (https://www.aliexpress.com/item/1005001275429959.html)

•Upgrade parts combine (https://www.aliexpress.com/item/1005002019863241.html)

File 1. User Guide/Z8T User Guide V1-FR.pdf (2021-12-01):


# Modèle : Z8TLa 3ème génération Z8

# Mode d'emploi

# Lien de téléchargement des documents les plus récents :

# https://github.com/ZONESTAR3D/Z8T

# Liste de colisage

1 | 2 | 3 | 4 | 5 | 6 | 7


Non. | Nom | Vérifier | Non. | Nom | Vérifier
1 | Module de base | □ | 8 | Panneau de commande | □
2 | Tête d'impression avec support | □ | 9 | Pièces pour extrudeuse Titan avec support | □
3 | Modules moteur axe Z | □ | 10 | Vis, BUTÉES, Raccord, Tube PTFE, courroie, serre-câbles, etc. | □
4 | Vis-mère et Profils | □ | 11 | Support de rouleau de filament | □
5 | Moteurs pas à pas pour extrudeuse | □ | 12 | Câble USB et cordon d'alimentation | □
6 | transporteur Z (gauche) | □ | 13 | Outils | □
7 | transporteur Z (à droite) | □ | 14 | Carte SD / filament cadeau | □

8 14

9 | 11 | 12 | 13 10

# Assembler l'extrudeuse Titan (3 ensembles au total)


## Veuillez vous référer au guide vidéo pour l'installation :https://www.youtube.com/watch?v=VUR70xm5ZmA&t=21s

## Veuillez faire attention aux étapes ci-dessous lorsque vous l'installez :

### Essayez de vous déplacer vers ce La distance est d'environ 1,5 mm coin avant de le fixer

### Réglez d'abord la pression à la valeur médiane

# Installer les pièces de l'axe Z

2040V profils; Module moteur Z; Environ 22 mm; Diamètre:

HM4x25 signifie :
Vis à six pans creux
Longueur: 25mm

Installer les profils Z à la base

Installer le module Zmotor sur les profils Z

Installez le module Z ENDSTOPs sur le côté des profils Z

# Installer les pièces de l'axe Z

Installer les silders Z; Installer des vis sans fin; À travers l'écrou de cuivre; Verrouillé sur l'accouplement

Remarque : Ajustez les
colonnes excentriques
pour qu'elles
maintiennent bien le
rail et se déplacent en
douceur.

Installer le profil supérieur

Il y a deux trous sur
le profil supérieur

# Installer les pièces de l'axe X

Profil X; Garder la même hauteur

Disposition du câble hotend

Faites glisser le hotend de droite à gauche

# Installer la ceinture X

## Courroie de


## distribution

## Hotend (le hotend être caché dans cette image)

### Ajustez les colonnes

excentriques,

### laissez-le sur la position la plus lâche

### Utilisez 2 attaches de câble pour fixer la ceinture sur le support de hotend

### Move it to the left before fix the belt

### Move it to the right after fixed the belt

### Installer la ceinture X

### Comment serrer la ceinture X

# Installer les autres pièces


Installez l'écran LCD à droite/en bas de l'imprimante | Installez le chargeur d'extrusion sur le dessus du cadre

### Installez le support du rouleau de filament sur le dessus du cadre

### REMARQUE : deux des canaux sont fermés par l'outil de nettoyage à chaud lorsque l'imprimante a quitté l'usine

### Connectez le chargeur d'extrusion avec la tête d'impression par le guide de filament (tube PTFE)

# Ajuster la hauteur des Z ENDSTOP

Étape 1 : Ajustez les 4 écrous à main sous le foyer, laissez le foyer est parallèle au profil


inférieur.

Étape 2: faites pivoter manuellement les accouplements sur les deux moteurs de l'axe Z, laissez la buse toucher le foyer.

Étape 3 : Remontez le ENDSTOP, laissez sa partie ROUGE toucher la poulie du porteur.

1

2

2


Retirez le papier | Coller sur le foyer

# REMARQUE:

Faites attention lors du collage, évitez l'influence des bulles d'air car le lit chaud n'est pas lisse.

# Des astuces:

Déchirez d'abord un côté de l'autocollant au dos, puis nivelez avec une pelle d'un côté à l'autre, puis arrachez progressivement l'autocollant au dos.

# !!ATTENTION!!

# Faites attention lors de l'installation, pour éviter les risques de choc électrique !

# Vérifiez bien le câblage ! UN CÂBLAGE INCORRECT PEUT ENDOMMAGER L'APPAREIL ÉLECTRONIQUE !

# Réglez l'interrupteur 110V/220V (sur le côté de l'alimentation) sur la bonne position en fonction de la tension d'alimentation de votre ville !

# Placez le fil du moteur dans les rainures du profilé et recouvrez-les d'un couvercle de profilé en plastique et utilisez un serre-câble

pour envelopper les fils libres.

# Arrêtez immédiatement de travailler si le moteur a des vibrations ou des bruits anormaux, sinon les modules de commande peuvent être endommagés ! Assurez-vous que le ventilateur de refroidissement du hotend fonctionne lorsque la température de la buse est supérieure à 60

degrés, sinon vérifiez à nouveau le câblage.

# DC-IN, HOTBED a un courant de fonctionnement plus important, veuillez vous assurer que ces fils sont bien en

contact avec le terminal.

# Il est très important de vérifier la machine avant de la mettre sous tension. Cela peut éliminer les problèmes causés par certains matériels pour assurer une impression fluide!

## Étape 4: Déplacez manuellement le hotend et le hotbed pour voir si le mouvement est

fluide, sinon, ajustez l'écrou excentrique jusqu'à ce que le moteur se déplace en douceur. Reportez-vous à la procédure d'installation.

Étape 3: Déplacez le hotend et le hotbed vers leurs positions respectives de fin de course pour vérifier si le contact est bon et si le son est clair. Sinon, veuillez vérifier le fin de course et le remonter.

Étape 7: Faites pivoter manuellement la tige de vis de l'axe z pour vérifier si le contact de fin de course de l'axe z est fiable.

Étape 5: Vérifiez si la courroie d'entraînement des axes X et Y est fermement installée. S'il est trop lâche, essayez de le serrer.

## Étape 6: Vérifiez si la tige de vis est assemblée en place et si la vis est serrée

Étape 1 : veuillez vérifier si la poulie de synchronisation de l'axe XY est fixée sur l'arbre du moteur et si les accouplements sont fixés sur l'arbre des moteurs Z.

Étape 2: veuillez vérifier si les vis mères ont été fixées sur l'arbre d'accouplement.

# À propos des pièces électroniques

X MOTOR et X SW; Y MOTOR et Y SW; Z1 MOTOR et Z1 SW; Moteurs d'extrudeuse; Hotend; cooling FAN; Z2 MOTOR et Z2 SW; Y MOTOR; AC POWER Changer; AC POWER Connecteur; Control board cooling FAN; 110V/220V Changer; prise de carte

Push power button

See from left

Bed leveling Sensor

NOTE: Y SW can be installed
to the right side too

Voir de droite

Panneau de commande

Bouton du panneau de configuration

HOTBED

prise USB

# Photos de câblage

# Avant la mise sous tension, veuillez ouvrir le boîtier de commande et vérifier le


# câblage : 1. Tous les connecteurs sont bien connectés

2. Tous les modules de commande de moteur sont bien branchés dans la prise.

# Schéma de câblage


X Motor Driver Module | Y Motor Driver Module | Z1 Motor Driver Module

Z2 Motor Driver
Module

#1 Extruder Motor

Driver Module

#2 Extruder Motor

Driver Module

#3 Extruder Motor

Driver Module

# Disposition des fils/câbles

VUE DE DESSOUS | VUE ARRIÈRE

Hotbed cable; HOTEND Cable; X Motor+SW cable

X Motor + SW cable
HOTEND Cable
Z1 Motor + SW cable

EXT1 Motor + SW cable
EXT2 Motor cable
EXT3 Motor cable

Z2 Motor+SW cable

Y Motor + SW cable

Mettez le fil du moteur
dans la rainure du
profil et couvrez-le par
le couvercle du profil

Attendez que l'écran LCD s'éteigne; POWER OFF; Faites « Éteindre l'alimentation » sur l'écran LCD; Éteignez l'interrupteur d'alimentation secteur; Branchez le cordon d'alimentation; Allumer l'interrupteur d'alimentation secteur; Appuyez et maintenez enfoncé le bouton d'alimentation CC; Jusqu'à ce que l'écran LCD affiche "ZONESTAR"; POWER ON

### Mise hors tension automatique après impression

## Si vous souhaitez que l'imprimante s'éteigne automatiquement lorsque l'impression est

terminée, vous devez ajouter une commande M81 au code de fin lors du tranchage.

## REMARQUE: Fonctionne uniquement lors de l'impression à partir d'une carte SD !

# Menu LCD et fonctionnement


Fonctionnement du bouton : <Rotation dans le sens des aiguilles d'une montre> : Article suivant / Valeur +. <Rotation dans le sens inverse des aiguilles d'une montre> : Article précédent / Valeur -. <Pousser> : Entrer / Exécuter.

### Message d'état

### Heure imprimée

### Taux de progression de l'impression

### Vitesse du ventilateur de l'extrudeuse

### Position actuelle

### Vitesse d'impression

## Pour plus de détails sur le menu LCD, veuillez vous référer à "Description du menu

LCD12864.pdf".

### Actuel VTOOL

### Taux de mélange E1:E2:E3

### ICÔ NE

### Température de la buse

### Nozzel

### Température actuelle

### Réglage de la température

### Hotbed

### Température actuelle

Une fois l'assemblage et le câblage terminés, veuillez suivre les étapes ci-dessous pour vérifier.

### Étape 1: Avant de mettre l'appareil sous tension, confirmez à nouveau:

✓ | Vérifiez s'il a été correctement réglé sur le sélecteur de tension d'alimentation 110V/220V.
✓ | Vérifiez si les composants sont correctement connectés. En particulier, DC+ et DC- de l'alimentation DC ne se sont pas inversés, le
| câblage est en bon contact avec les bornes et aucun fil n'est court-circuité.
✓ | Vérifiez si le câble de l'écran LCD est bien connecté au connecteur EXP1.

### Étape 2: Vérifiez le capteur de température:

Branchez le cordon d'alimentation secteur et allumez l'alimentation secteur, regardez l'écran LCD, la température doit être presque la même

que la température ambiante.

### Étape 3: Vérifiez les moteurs des axes X, Y et Z et les BUTÉES

FAIRE: Motion>>Move axis>>Move X/Y/Z>> Move 10mm. Entrez et tournez le bouton pour déplacer l'axe X/Y/Z..
CHÈQUE : Vérifiez si la tête d'impression peut se déplacer vers la gauche/droite (axe X), avant/arrière (axe Y) ou si le foyer peut se
| déplacer vers le haut/bas (axe Z).
CHÈQUE : Appuyez sur le fin de course X/Y et maintenez-le enfoncé et essayez de réduire la valeur de Move X/Y, la tête d'impression
| devrait s'arrêter de bouger, sinon vérifiez la connexion du fin de course X/Y..
CHÈQUE : Appuyez et maintenez enfoncé l'interrupteur de fin de course Z et essayez de réduire la valeur de Move Z, le foyer devrait
| s'arrêter de bouger, sinon vérifiez la connexion de l'interrupteur de fin de course Z.

Température de la buse; Foyer Température

### Étape 4: Vérifier les radiateurs et les ventilateurs:

1. Temperature>>Nozzle: 180, réglez la température de la buse à 180 degrés, puis revenez au menu d'informations, la température de la buse augmentera, elle est généralement d'un degré par seconde environ.
2. Temperature>>Bed: 60, réglez la température du lit chauffant à 60 degrés, puis revenez au menu d'informations, la température du lit chauffant augmentera, elle est généralement d'un degré toutes les 2 secondes environ.
3. Vérifiez le ventilateur de refroidissement HOTEND: Lorsque la température de la buse dépasse 60 degrés, le ventilateur de refroidissement sur le côté de la tête d'impression doit fonctionner.
4. Vérifiez le ventilateur de l'extrudeuse, Temperature>>Fan Speed: 100%, le ventilateur de l'extrudeur devrait fonctionner.

Extruder fan work; HOTEND cooling fan work When nozzle temperature over 60 degree

### Étape 5: Vérifiez les mangeoires d'extrusion :


1. Temperature>>Nozzle: 180, réglez la température de la buse à 180 degrés, puis revenez au menu info, en attendant que la température atteigne le réglage.
2. Mixer>>Set Mix>>Active V-tool: 0>> set to Active V-tool: 3. Réglez le rapport de mélange de toutes les extrudeuses sur le même (33:33:34).
3. Move Axis>>Extruder>>Move 10mm>>Extruder: +20mm, surveillez l'engrenage du distributeur d'extrusion et vérifiez si tous les distributeurs d'extrusion fonctionneront.

Gear Rotate

# Dépannage rapide

L'écran LCD ne s'affiche pas après la mise sous tension | 1. Le rétroéclairage de l'écran LCD ne s'allume pas. Raisons possibles : Le cordon d'alimentation secteur n'est pas branché ; DC+ et - sont inversés ; la prise de courant est débranchée de l'alimentation électrique. 2. Le rétroéclairage de l'écran LCD s'allume mais n'a pas de caractères. Raisons possibles : le câble LCD est inversé; erreur de micrologiciel ou perdu;

### Erreur de température

Le moteur ou l'alimentateur d'extrusion ne fonctionne pas correctement | 1. L'alimentation ne fonctionne pas (Remarque : l'USB peut également fournir une alimentation de +5 V et laisser l'écran LCD afficher, mais ne peut pas alimenter les moteurs et le chauffage). 2. Le câble du moteur est débranché. 3. Le module d'entraînement du moteur ne s'est pas bien connecté à la prise de la carte de commande. 4. Chauffer la buse à plus de 150 degrés avant l'extrusion.
Erreur de direction du moteur | 1. Le moteur n'est pas connecté au bon connecteur de la carte de commande, comme les prises X et Y échangées. 2. L'ordre des fils du câble moteur est incorrect. 3. La version du micrologiciel est incorrecte.
Problème de fin de course (ENDSTOP) | 1. Le fil de l'interrupteur de fin de course est déconnecté de la carte de commande. 2. L'interrupteur de fin de course est connecté au mauvais connecteur, par exemple, a échangé les interrupteurs de fin de course X et Y. 3. Le fil est déconnecté avec le fin de course. 4. Vérifiez le signal de l'interrupteur de fin de course, il doit être connecté aux broches « S » et « GND » du connecteur sur la carte de contrôle.

### Le capteur de température Hotend ne se connecte pas bien

### Le capteur de température du foyer ne se connecte pas bien

1. L'imprimante redémarre automatiquement lors du chauffage du lit chauffant ou de la buse. Vérifiez si le commutateur de sélection de tension d'alimentation CA est correctement réglé et si le câble d'alimentation CC est bien connecté.
2. Hotend ne peut pas être atteint à la température de réglage. Vérifiez si la thermistance est absente du bloc chauffé. Vérifiez si le câble chauffant de la tête d'impression est bien connecté.
3. Le foyer ne peut pas être atteint à la température réglée. A) Vérifiez si le câblage est bien connecté. B) Vérifiez si la température ambiante est inférieure à 5 degrés.

### Problème de lit chauffant et hotend

# Préparez-vous à imprimer - nivelez le foyer

Nettoyer la buse : assurez-vous qu'il n'y a pas de filament au bout de la buse, sinon, retirez-le

## à l'aide d'une pince diagonale. 1

2

3

Exécuter “Motion>> Auto Home”, attendez que le hotend revienne à la position d'origine.

Surveillez la buse et assurez-vous que la buse est plus haute que le lit, sinon serrez les écrous à main sous le lit pour abaisser le foyer ou desserrez ces écrous pour remonter le lit.

4

Exécuter “Motion>> Level Corners”, la buse ira dans les coins, ajustez les écrous à main sous le foyer, laissez la buse toucher presque le foyer. Afin d'obtenir une distance correcte, vous pouvez mettre un papier A4 sur le foyer, et lorsque la distance entre la buse et le foyer ne peut insérer qu'un papier, ce sera parfait.

Choisir “next corner”, et ajustez à nouveau. Répétez cette étape encore et encore,

## jusqu'à ce que tous les quatre coins soient à la même hauteur. 5

# Préparez-vous à imprimer - Chargez le filament

## Buse de préchauffage: Temperature>> Nozzle, réglez-le à environ 180 degrés (pour le PLA)

ou 220 degrés (pour le filament PETG), puis la buse sera chauffée. Attente de la température de la buse atteinte au réglage.

1

2

Appuyez sur la poignée du chargeur d'extrusion et insérez le filament jusqu'à ce que le filament entre dans la hotend.

## Exécuter “Motion>> Move axis>>Extruder>>Move 1mm>>extruder: ****mm”, puis tournez

lentement le bouton dans le sens des aiguilles d'une montre, jusqu'à ce que vous puissiez voir que le filament s'écoule de la buse.

3

REMARQUE: Nous vous recommandons fortement de commencer avec une seule couleur.

## Lorsque le produit quitte l'usine, nous avons fermé deux canaux avec outils de nettoyage hotend. Vous pouvez utiliser le canal qui n'est pas fermé pour imprimer vos premières œuvres !


1

Insérez la carte SD dans la prise pour carte SD du boîtier de commande, puis allumez le boîtier de commande.

2

Exécuter “Print from Media”>> Choose “Test_gcode\Single Color\xyz_cube.gcode”, appuyez sur le bouton pour lancer l'impression.

3

Attendez que l'imprimante ait fini de chauffer et commencez à imprimer, surveillez la distance entre la buse et le lit, double-cliquez sur le bouton du menu LCD et réglez le décalage z si la distance n'est pas parfaite, laissez le filament bien coller sur le foyer.

Carte SD enfichable | Ajuster le décalage Z | Attendez la fin de l'impression !
| Trop près

# More

# 1. À propos du tranchage :

Vous devez convertir le fichier objet 3D (stl, obj, amf, etc.) en un fichier gcode avant de

## l'imprimer, ceprocessus est appelé tranchage. Pour savoir comment découper un fichier de

modèle 3D, veuillez vous référer à ce guide “Slicing guide for mixing color printer.pdf”.

# 2. Nivellement automatique du lit :

## Cette imprimante est équipée d'un capteur de proximité pour le nivellement automatique

du lit chaud. Avecce capteur, vous pouvez corriger les irrégularités du lit chaud. À propos de plus d'informations, s'il vous plaîtreportez-vous à ce guide : “Auto leveling feaure user guide (PL-08N).pdf”.

# 3. Fonctionnalité de mélange de couleurs:

## Cette machine est équipée d'un mélangeur de couleurs, qui peut imprimer une seule couleur, plusieursobjet de couleur. Pour l'introduction de l'impression de couleurs

mélangées, veuillez vous référer à ceguider:“Operation guide for mixing color printer.pdf”.

# 4. Fonction de récupération de perte de puissance :

## Lorsque vous imprimez à partir d'une carte SD et que l'alimentation est perdue lors de l'impression, l'imprimante reprendra l'impression à partir de la dernière couche imprimée avant la perte d'alimentation automatiquement, pour les détails, veuillez vous référer à

ce guide : “Power loss recover feature.pdf”.

# Vous pouvez imprimer quelque chose pour mettre à niveau votre imprimante, nous avons fait une partie imprimée et stocké le fichier stl sur la carte SD, vous pouvez vous sentir libre de le découper et de l'imprimer, puis de les installer dans votre

kit pour rendre l'imprimante meilleure .


cap_af_20v.stl | cap_af_40v.stl | cap_m4nut.stl


# lcd12864_case_v2.stl

Vous pouvez ajouter plus de fonctions à la machine en ajoutant des accessoires,

# notamment :

# 32 bits control board (https://www.aliexpress.com/item/1005001300737027.html)

4.3" TFT (https://www.aliexpress.com/item/1005002378065646.html)- (https://www.aliexpress.com/item/1005002378065646.html)LCD screen (https://www.aliexpress.com/item/1005002378065646.html)

# Silent motor driver (https://www.aliexpress.com/item/4000596369015.html)

# Filament run out detector(FROD) (https://www.aliexpress.com/item/4001309957376.html)

# 3D Touch bed leveling sensor (https://www.aliexpress.com/item/1005001464420529.html)

# Magnetic flexible hot bed sticker (https://www.aliexpress.com/item/4000793898821.html)

# Hotbed glass (https://www.aliexpress.com/item/4001317243160.html)

# Hotbed Nuts (https://www.aliexpress.com/item/4000726717520.html)

# Z lead screw fix module (https://www.aliexpress.com/item/1005002401708373.html)

3 (https://www.aliexpress.com/item/1005001275429959.html)- (https://www.aliexpress.com/item/1005001275429959.html)IN (https://www.aliexpress.com/item/1005001275429959.html)- (https://www.aliexpress.com/item/1005001275429959.html)2 (https://www.aliexpress.com/item/1005001275429959.html)- (https://www.aliexpress.com/item/1005001275429959.html)OUT hotend

3 (https://www.aliexpress.com/item/1005001275429959.html)- (https://www.aliexpress.com/item/1005001275429959.html)IN (https://www.aliexpress.com/item/1005001275429959.html)- (https://www.aliexpress.com/item/1005001275429959.html)3 (https://www.aliexpress.com/item/1005001275429959.html)- (https://www.aliexpress.com/item/1005001275429959.html)OUT hotend (https://www.aliexpress.com/item/1005001275429959.html)

# Upgrade parts combine (https://www.aliexpress.com/item/1005002019863241.html)

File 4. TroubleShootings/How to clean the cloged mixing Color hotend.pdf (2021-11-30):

# How to clean the clogged mixing-color hotend

Step 1: Heat the hot end (nozzle) to 200 degrees and wait for the temperature to be reached

### Step 2: Remove the fitting and pull out the filament (Figure 1)

Tips 1: If it is difficult to pull out the filaments, you can use the cutting pliers to clamp the filaments and pull out (Figure 2)

Tips 2: If the filaments cannot be pulled out at all, you can use cutting pliers to cut the filaments

### Step 3: Remove the nozzle from the hot end

Note: Please pay attention to prevent burns, it is recommended to wear heat-resistant gloves for operation.

Step 4: Install the hotend-clean-tool on the hot-end (Figure 3), close the channels that are not blocked, and leave only the blocked

channel.

Tips: If the hot end is blocked by filaments and cannot be inserted into the hotend-clean-tool, you can use a lighter to heat the

thin rod of the hotend-clean-tool, and then insert it to the hotend(Figure 4).

Step 5: Manually feed in at least 50cm filaments slowly from the hotend (Figure 5).
Step 6: Clean the filaments in front of the hotend (Figure 6) . If necessary (there are other channels are blocked), you can close the

cleaned channel with a “hotend cleaning tool” before cleaning the next channel.

Step 7: Install the nozzle back.


Figure 1 | Figure 2 | Figure 3 | Figure 4 | Figure 5 | Figure 6

# Why the hotend be clogged

There are many reasons that may cause the hoend to be blocked. Here are some common reasons:

### - Incorrect slicing settings (Figure 7)

Tips: Check the settings in slicing software, to disable “Extruder/Nozzle switching retraction”. For example, set “Nozzle Switch Retraction Distance” to 0 in Cura.

### - Incorrect filament loading

Tips 1: When loading the filament to the hotend, please make sure that the filament enter the heating block of the hot end, it is about 45mm deep into the hot end.

Tips 2: It is recommended to use the “hotend cleaning tool” to close the unused channels of the hotend.

### - Damaged nozzles

Tips: In addition to complete clogging (consumables cannot flow out of the nozzle), the nozzle may also be partially clogged. If you find the filament flowed out from the

nozzle is thinner than normal, the nozzle may be partially clogged. If this happens, you need to use a nozzle cleaning needle to clean the nozzle or replace a new

nozzle directly.

### - The nozzle are too close to the printing platform

Question: If the nozzle is too close to the hot bed when printing the first layer, the filament may not be ejected. If this is maintained for a long time, it may cause the

filament in the hot end to be over-compressed and cause blockage (often blocked at the entrance of hotend).

Solution: Set first layer height = 0.3~0.4mm; heat bed temperature = 70 degrees(PLA); the printing speed 15mm/s (or 50%); Choose “Raft” on “Build Plate Adhesion”

to help filament sticker on the hotbed.

### - Mix different types of filament

Tips 1: Unexpected problems may occur when different types of materials are mixed. It is recommended to use a manual extrusion test before printing large

objects to confirm that the filaments can be extruded normally after mixing.

Tips 2: Before starting to print, extrude some filaments to confirm that the filament can flow out normally.

### - The hot end is overheated

Tips : The overheated hot end may easily cause the hot end to be blocked. Be careful to keep the working temperature of the hot end radiator not exceeding 60

degrees, especially when printing PLA materials. If the hot end is overheated, check the cooling fan and the ambient temperature of the hot end.


### Figure 7

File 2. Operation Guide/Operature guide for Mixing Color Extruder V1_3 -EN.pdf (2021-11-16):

# Operation Guide for Mixing Color Extruder

V1.3

## For the 4

## th version M3 and M4 hotend

2

# Structure and Working principle

## •Structure of mixing color hot end

Fittings To fix the PTFE tube on the hotend; Heat sink Connect the hotend to the printer keep the inner PTFE tube is cool; Inner PTFE tube (Ø 4x2 PTFE tube); Filament guide(Ø 4x2 PTFE Tube); Heat-insulating block; Heating block To melt and mix the filament; Nozzle MK7/MK8 nozzle; Filament; Mixing Room

Isolation the throat with filament to keep the filament cool

To connect the extrusion feeder and hotend

To isolate the heating block from the heat sink

A 50W Cartridge Heater is used for heating A thermistor is used to measure temperature

## •Color mixing principle:

1. Filaments melt and mix in the mixing room, and then flow out from the nozzle.
2. To change the feed ratio, it can get different color filament.

# !!ATTETION!!


## DO NOT load / unload filament when the nozzle temperature is less than 150℃

DONOT feed-in filament over 10mm if any of the channels is empty, otherwise may cause it be clogged. You can:
1. Load filament to all channels.
2. Use a hotend clean tool to close empty channels.


# How to print single color 3d object


Step 1: Refer to the silcing guide for mixing color printer to covert the 3d mode file to gcode file.
Step 2: Preheat the nozzle to about 170 degree
Step 3: Use hotend clean tool to close the unused channle of hotend
Step 4: load filament to the hotend. NOTE: For M4 printer, recommend to load the filament to the center Channel, and use “hotend clean tool” to close the others channels.
Step 5: print gcode file from SD card

# Change print color by adjust mixing rate (LCD12864)

Step 1. Start to print a singel color gcode file(Vase.gcode) from SD card.


Step 2. For LCD12864 screen, set on the menu>>
●Mixer>>Active V-tool: Select the vtool currently printed, or use the default value,

the range is 0 ~ 15.
●Mixer>>Mix>>Component1~3(4 for M4): Arbitrarily adjust the percentage of extruder 1~3(4 for 4), range is 0 ~ 100.
●Mixer>>Mix>>Comit V-tool Mix: Redistribute the percentage of all extruders in proportion

and send it to the current vtool.

After setting up, on the ideal menu shows VTOOL:0

# How to realize gradient mix print (LCD12864)


Step 1. Start to print a singel color gcode file(Vase.gcode) from SD card.
Step 2. For LCD12864 screen, set on the menu>>

Mixer>>Gradient: disable >>

>> Start Z: set the start Z heigth (such as:0mm)

>> End Z: set the END Z heigth (such as:200mm)

>> Start V-tool: set the start V-tool (such as:0)

>> End V-tool: set the end V-tool (such as:1)
After set Start Z isn’t equal to the End Z, and Start V-tool isn’t equal to End V-tool, the LCD will shows “Gradient : enable” and on the ideal menu shows gradient


# How to realize random mix print (LCD12864)

Step 1. Start to print a singel color gcode file(Vase.gcode) from SD card.


Step 2. For LCD12864 screen, set on the LCD menu>>

Mixer>>Random Mix: disable >>

Start Z: set the start Z heigth(such as:0mm) End Z: set the END Z heigth(such as:200mm)


Height: set interval distance(such as:10mm), When the z-axis distance changes beyond

this value, the mixing ratio changes randomly once.

Extruders: set the number of extruders with random variation(such as:4)
After set Start Z isn’t equal to the End Z, the LCD will shows “Gradient : enable”

and on the ideal menu shows random


# Change print color by adjust mixing rate (LCD-DWIN)

Step 1. Start to print a singel color gcode file(Vase.gcode) from SD card.
Step 2. For TFT screen, set on the menu>>
●Mixer>>Current V-TOOL: Select the vtool currently printed, or use the default value, range is 0 ~ 15.

●Mixer>>Mix>>Extruder1~3(4 for M4): Arbitrarily adjust the percentage of extruder 1~4, range is 0 ~ 100.

●Mixer>>Mix>>Comit V-tool: Redistribute the percentage of all extruders in proportion and send it to the

current vtool. The current vtool value changes color.
After setting up, enter printing, on the printing menu shows: Mix 0


# How to realize gradient mixing print (LCD-DWIN)

Step 1. Start to print a singel color gcode file(Vase.gcode) from SD card.
Step 2. For LCD-DWIN screen, set on the menu>>

Mixer>>Gradient: OFF >>

>> Start Z: set the start Z height (such as:0mm)

>> End Z: set the END Z height (such as:200mm)

>> Start V-tool: set the start V-tool (such as:0)

>> End V-tool: set the end V-tool (such as:1)
After set Start Z isn’t equal to the End Z, and Start V-tool isn’t equal to End V-tool, the LCD will shows “Gradient : ON” and on the printing menu shows: Gradient 0--->1


# How to realize random mixing print (LCD-DWIN)

Step 1 Start to print a singel color gcode file(Vase.gcode) from SD card.
Step 2. For LCD-DWIN screen, set on the menu>>

Mixer>>Random: OFF >>

>> Start Z: set the start Z height (such as:0mm)

>> End Z: set the end Z height (such as:200mm)

>>Height: set interval distance (such as:10mm), When the z-axis distance changes beyond this value, the mixing

ratio changes randomly once.
Extruders: set the number of extruders with random variation (such as:4)
After set Start Z isn’t equal to the End Z, the LCD will shows “Random : ON” and on the printing menu shows:

Random


# How to realize gradient Random mixing by modifing Add gcode)

You can also add a M166/M167 command into the gcode file to apply gradient / random mixing printing, so it can

automatically work when print from SD card.

Gradient Mixing:
For example: M166 S1 A0 Z200 I0 J1
S1→Enable gradient mix A0 → startZ is 0mm Z200 → EndZ is 200mm I0 → Start V-tool is 0 J1 → End Vtool is 1

Random Mixing:
For example: M167 S1 A0 Z100 H0.2 E3
S1→Enable Random mix A0 → startZ is 0mm Z100 → EndZ is 100mm H0.2 → change color every 0.2mm height
E3 → 3 extruders (E0~E2) will be used to mix

Please note that there is no Tn(T0 ~ T16) command after M166/M167 command in the gcode code, because it will stop automatic gradient/Random mixing function

/**
* M167: Start a random mixing
* S[bool] - Enable / disable random mixing
* A[float] - Starting Z for the random mixing
* Z[float] - Ending Z for the random mixing
* H[float] - Minimum height of changing mixing rate * E[int] - how many extruders used on random mixing * */

/**
* M166: Start a gradient mix
*
* S[bool] - Enable / disable gradients
* A[float] - Starting Z for the gradient
* Z[float] - Ending Z for the gradient.
* I[index] - V-Tool to use as the starting mix. * J[index] - V-Tool to use as the ending mix. **/

# How to print multi-color 3d object

Step 1: Refer to the silcing guide for mixing color printer to covert the 3d mode file to gcode file.
Step 2: Preheat the nozzle to about 170 degree
Step 3: Load filament to the hotend, and use hotend clean tool to close the unused channles
Step 4: print gcode file from SD card(4C_Niko_Dog.gcode)

TIPS 1:
Make a mark on the extrusion feeder in order to quickly distinguish the extruder
PS: Their sequence depends on wiring


TIPS 2: Recommended channels for different quantities of filaments

TIPS 3:
The steps to load filaments:


1. Heat nozzle, and then use hotend clean tool to close unused channel (remove the fittings first)!
2. load all of the filaments into the hotend, stop when it enter the hotend about 30~40mm.
3. MENU>>Motion>>Move axis>>Set V-TOOL to 3(for M3) or 4(for M4).
4. MENU>>Motion>>Move axis>Extruder>> feed until the filament flow from the nozzle

# How to slicing multi-color 3d object

# About how wo slicing, please refer to the guide in this link: https://github.com/ZONESTAR3D/Slicing-Guide


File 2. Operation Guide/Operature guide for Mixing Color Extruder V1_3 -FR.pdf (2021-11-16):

# Guide d'utilisation pourextrudeuse de couleur de mélange

V1.3

## Pour la 4ème version M3 et M4 hotend

2

# Structure et principe de fonctionnement

## •Structure de mélange de couleur hot end

Raccords Pour fixer le tube PTFE sur la hotend; Dissipateur de chaleur Connectez le hotend à l'imprimante; Tube intérieur PTFE (tube Ø 4x2 PTFE); frais; Guide de filament (Tube Ø 4x2 PTFE); bloc calorifuge; Bloc chauffant Faire fondre et mélanger le filament; Buse MK7/MK8 type; Filament; Salle de mixage

garder le tube intérieur en PTFE au frais

Isolation de la gorge avec filament pour garder le filament au

Pour connecter le chargeur d'extrusion et la hotend

Pour isoler le bloc chauffant du dissipateur thermique

Un chauffe-cartouche de 50 W est utilisé pour le chauffage Une thermistance est utilisée pour mesurer la température

## •Principe de mélange des couleurs:

1. Les filaments fondent et se mélangent dans la salle de mélange, puis s'écoulent de la buse.
2. Pour changer le rapport d'alimentation, il peut obtenir un filament de couleur différente.

# !!ATTETION!!


## NE PAS charger/décharger le filament lorsque la température de la buse est inférieure à 150℃


N'introduisez PAS de filament de plus de 10 mm si l'un des canaux est vide, sinon cela pourrait le boucher. Vous pouvez:
1. Chargez le filament sur tous les canaux.

### 2. Utilisez un « outil de nettoyage hotend » pour

fermer les canaux vides.

# Comment imprimer un objet 3D monochrome

Étape 1 : reportez-vous au guide de silcing pour mélanger l'imprimante couleur pour convertir le fichier de mode 3D en fichier gcode.
Étape 2: préchauffer la buse à environ 170 degrés

Étape 3: Utilisez l'outil de nettoyage hotend pour fermer le canal inutilisé de hotend

Étape 4 : chargez le filament sur la hotend. REMARQUE : pour l'imprimante M4, il est recommandé de charger le filament au centreChannel, et utilisez "hotend clean tool" pour fermer les autres canaux.
Étape 5 : imprimer le fichier gcode à partir de la carte SD


## Changer la couleur d'impression en ajustant le taux de mélange (LCD12864)

Étape 1. Commencez à imprimer un fichier gcode couleur unique (Vase.gcode) à partir de
la carte SD.
Étape 2. Pour l'écran LCD12864, réglez sur le menu>>


●Mixer>>V-tool actif : sélectionnez le vtool actuellement imprimé ou utilisez la valeur par défaut,la plage est de 0 ~ 15.
●Mixer>>Mix>>Component1~3(4 for M4) : ajustez arbitrairement le pourcentage de l'extrudeur 1~3(4 for M4),la plage est de 0 ~ 100.
●Mixer>>Mix>>Comit V-tool Mix : redistribuez le pourcentage de tous les extrudeurs en proportionet l'envoyer au vtool actuel.

Après la configuration, sur le menu idéal affiche VTOOL:0

# Comment réaliser l'impression en dégradé (LCD12864)

Étape 1. Commencez à imprimer un fichier gcode couleur unique (Vase.gcode) à partir de la carte SD.
Étape 2. Pour l'écran LCD12864, réglez sur le menu>>


Mixer>>Gradient: disable
>> Start Z: définissez la hauteur de début Z (par exemple: 0 mm)

>> End Z : définissez la hauteur de FIN Z (par exemple : 200 mm)

>> Start V-tool: définissez le V-tool de début (par exemple : 0)

>> End V-tool : définissez le V-tool de fin (par exemple : 1)
Après avoir défini Start Z n'est pas égal à End Z, et Start V-tool n'est pas égal à End Vtool,l'écran LCD affichera « Gradient : enable » et sur le menu idéal affichera le dégradé

# Réalisez la couleur de mélange aléatoire(LCD12864)


Étape 1. Commencez à imprimer un fichier gcode couleur unique (Vase.gcode) à partir de la carte SD.
Étape 2. Pour l'écran LCD12864, réglez sur le menu>>

Mixer>>Random Mix: disable >>

>>Start Z: définissez la hauteur de début Z (par exemple: 0 mm)

>> End Z : définissez la hauteur de FIN Z (par exemple : 200 mm)
>> Height: définissez la distance d'intervalle (par exemple : 10 mm), lorsque la distance de l'axe z change au-delà de cette valeur, le rapport de mélange change de manière aléatoire une fois.

>> Extruders: définir le nombre d'extrudeuses avec une variation aléatoire (par exemple:3)

Une fois que le début Z défini n'est pas égal à la fin Z, l'écran LCD affiche “Random : enable”

et sur le menu idéal affiche aléatoire.


## Changer la couleur d'impression en ajustant le taux de mélange (LCD-DWIN)

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

Étape 2. Pour l'écran TFT, définissez-le dans le menu>>

●Mixer>>Current V-TOOL : sélectionnez le vtool actuellement imprimé ou utilisez la valeur par défaut, la plage est de 0 à 15.
●Mixer>>Mix>>Extruder1~3(4 for M4) : ajustez arbitrairement le pourcentage de l'extrudeur 1~3(4 for M4), la plage est de 0 ~ 100.
●Mixer>>Mix>>Comit V-tool : redistribuez le pourcentage de tous les extrudeurs en proportion et envoyez-le auvtool actuel. La valeur vtool actuelle change de couleur.

Après la configuration, entrez dans l'impression, sur le menu d'impression affiche : Mix 0


# Comment réaliser l'impression en dégradé (LCDDWIN)

Étape 1. Commencez à imprimer un fichier gcode à une seule couleur (Vase.gcode) à partir de la carte SD.

Étape 2. Pour l'écran LCD-DWIN, définissez-le dans le menu>>

Mixer>>Gradient: OFF >>

>> Start Z: définir la hauteur Z de départ(par exemple:0mm)

>> End Z: définir la hauteur END Z (par exemple:200mm)

>> Start V-tool: définir le démarrage V-tool(par exemple:0)

>> End V-tool: définir la fin de V-tool (par exemple:1)

Une fois que Start Z n'est pas égal à End Z et que Start V-tool n'est pas égal à End V-tool, l'écran LCD affiche “Gradient : ON” et sur le menu d'impression affiche: Gradient 0--->1


# Réalisez la couleur de mélange aléatoire (LCD-DWIN)

Étape 1. Commencez à imprimer un fichier gcode à une seule couleur (Vase.gcode) à partir de la carte SD.

Étape 2. Pour l'écran LCD-DWIN, définissez-le dans le menu>>

Mixer>>Random: OFF >>

>>Start Z: définissez la hauteur de début Z (par exemple: 0 mm)

>> End Z : définissez la hauteur de FIN Z (par exemple : 200 mm)
>> Height: définissez la distance d'intervalle (par exemple : 10 mm), lorsque la distance de l'axe z change au-delà de cette valeur, le rapport de mélange change de manière aléatoire une fois.

>> Extruders: définir le nombre d'extrudeuses avec une variation aléatoire (par exemple:3)
Une fois que Start Z n'est pas égal à End Z, l'écran LCD affichera “Random : ON” et sur le menu d'impression affiche: Random


# Comment imprimer un objet 3D multicolore

Étape 1 : Reportez-vous au "guide de silcing pour mélanger l'imprimante couleur" pour convertir le fichier de mode 3D en fichier gcode.
Étape 2: préchauffer la buse à environ 170 degrés et chargez le filament sur le hotend et utilisez l'outil de nettoyage du hotend pour fermer les canaux inutilisés
Étape 3: imprimer le fichier gcode à partir de la carte SD

TIPS 1:
Faire un repère sur le convoyeur d'extrusion afin de distinguer rapidement l'extrudeur
NOTE: Toutes les extrudeuses sont équivalentes et leur nombre dépend du câblage


TIPS 2: Canaux recommandés pour différentes quantités de filaments

TIPS 3:
Les étapes pour charger les filaments :


1. Chauffer la buse, puis utiliser l'outil de nettoyage hotend pour fermer le canal inutilisé (retirer d'abord les raccords) !
2. chargez tous les filaments dans le hotend, arrêtez-vous lorsqu'il entre dans le hotend d'environ 30 ~ 40 mm.
3. MENU>>Mouvement>>Déplacer l'axe>>Réglez V-TOOL sur 3 (pour M3) ou 4 (pour M4).
4. MENU>>Mouvement>>Déplacer l'axe>Extrudeuse>> alimenter jusqu'à ce que le filament s'écoule de la buse

# Comment imprimer un objet 3D multicolore

# À propos de la façon dont wo slicing, veuillez vous référer au guide dans ce lien: https://github.com/ZONESTAR3D/Slicing-Guide


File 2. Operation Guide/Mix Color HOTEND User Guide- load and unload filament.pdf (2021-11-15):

## 混色热端进料退料和换料操作手册

## How to Load/Unload Filament for Mixing Color HOTEND

## как загружать и перевозить цветные горячие концы накала

## Cómo manipular un filamento térmico mezclado

## Como Carregar/Descarregar o Filé para Misturar Cor HOTEND

## Comment charger et décharger un fil d 'extrémité thermique mélangé

# How to unload filament

- 第1步，加热喷嘴并等待温度到达,PLA是200℃,PETG是230℃ (Fig 1)

### - 第2步: 操作菜单手动挤料直至耗材顺利从喷组流出 (Fig 2)

- 第3步: 操作菜单选择“Unload filament E1/E2/E3/E4”,然后压住挤出机手柄并拔出耗材(Fig 3)
- Step 1: Heating the nozzle, PLA to 200 ℃ PETG to 230 ℃. (Fig 1)
- Step2: Purg a little filament from all extruders, until the filament can flow out from nozzle well. (Fig 2)
- Step 3: Do “Unload filament E1/E2/E3/E4” from LCD MENU，then pull out filament from extrusion feeder. (Fig 3)
- первый шаг: нагревательная форсунка, PLA до 200℃ PETG до 230℃. (Fig 1)
- Второй этап: выжать немного волокна из всех экструдеров до тех пор, пока волокна не будут вытекать из сопла. (Fig 2)
- Этап 3: выполнение “Unload filament E1/E2/E3/E4”. вытащить нить накала из экструдера. (Fig 3)
- Primer paso: toberas de calentamiento, de PLA a 200℃ PETG a 230℃. (Fig 1)
- Segundo paso: sacar un poco de fibra de todas las máquinas de desplazamiento hasta que las fibras puedan salir por la abertura de la tobera. (Fig 2)
- Tercera etapa: ejecución del “Unload filament E1/E2/E3/E4” ， sacar la luz del encuadernador. (Fig 3)
- Passo 1: Aquecimento do bocal, PLA a 200℃ PETG a 230℃. (Fig 1)
- Step2: Purgar um pouco de filamento de todos OS extrusores, até que o filamento possa sair do poço do bocal. (Fig 2)
- Passo 3: Executar “Unload filament E1/E2/E3/E4”. Retirar o filamento do alimentador de extrusão. (Fig 3)
- Première étape: Tuyères de chauffage, PLA à 200℃ PETG à 230℃. (Fig 1)
- Deuxième étape: Extruder une petite quantité de filaments de toutes les extrudeuses jusqu 'à ce que les filaments sortent de l' orifice de buse. (Fig 2)
- Étape 3: mise en œuvre du menu LCD “Unload filament E1/E2/E3/E4”. étirez les fils du four d 'extrusion. (Fig 3)

# How to load filament

- 第1步，加热喷嘴并等待温度到达,PLA是200℃,PETG是230℃(Fig1)

### - 第2步，使用热端清理工具关闭未使用的热端的通道(Fig4) - 第3步，使用斜口钳剪将耗材头部剪成斜口(Fig5) - 第4步, 压住挤出机压头并将耗材插入,并一直将耗材送入热端内部(Fig6) - 第5步, 如果需要同时装入多种耗材,重复3和4 - 第6步, 操作菜单手动挤料直至耗材顺利从喷组流出. (Fig3)

- Step 1: Heating the nozzle, PLA to 200℃ PETG to 230℃. (Fig1)
- Step 2: Use the hotend clean tool to close ununsed channel. (Fig4)
- Step 3: Cut the head of the filament with a slant cutter. (Fig5)
- Step 4: Press the handle of extrusion feeder and insert the filament until it enter the hot end. (Fig6)
- Step 5: Repeat step 3 and 4 if you need to load more than one filament at the same time
- Step 6: Purg filament from all extruders, until the filament can flow out from nozzle well. (Fig3)
- первый шаг: нагревательная форсунка, PLA до 200℃ PETG до 230℃. (Fig1)
- Шаг 2: Закрытие неиспользованных каналов с помощью утилиты горячей очистки. (Fig4)
- Третий этап: резать патрон накала косым резаком. (Fig5)
- шаг четвертый: нажать рукоятку экструдера, вставить нить накала в горячий конец. (Fig6)
- Шаг 5: если необходимо одновременно загружать несколько нить накала, повторить шаги 3 и 4
- шаг шестой: экструзия из всех экструдеров длинных шёлков до тех пор, пока длинный шёлк не истечет из соплового отверстия. (Fig3)

# How to load filament

- Primer paso: toberas de calentamiento, de 200 a 200℃ PETG a 230℃. (Fig1)
- Medida 2: utilización de instrumentos de depuración de calor para cerrar canales no utilizados. (Fig4)
- Tercer paso: cortar la lámpara con un cortador oblicuo. (Fig5)
- Cuarto paso: presionar para sacar el mango del horno e insertar la lámpara en el extremo caliente. (Fig6)
- Medida 5: repetición de las etapas 3 y 4 si es necesario introducir simultáneamente varios filamentos
- Sexto paso: sacar alambre largo de todas las máquinas de desplazamiento hasta que el alambre pueda salir por la abertura de la tobera. (Fig3)
- Passo 1: Aquecimento do bocal, PLA a 200℃ PETG a 230℃. (Fig1)
- Passo 2: Use a ferramenta de limpeza hotend para Fechar o canal não aberto. (Fig4)
- Passo 3: Corte a cabeça do filamento com um alicate inclinado. (Fig5)
- Passo 4: Pressione o cabo do alimentador de extrusão e insira o filamento até Entrar Na extremidade Quente. (Fig6)
- Passo 5: Repetir o Passo 3 E 4 se você precisar carregar Mais de um filamento Ao Mesmo tempo.
- Passo 6: Extrair filamento de todos OS extrusores, até que o filamento possa sair do poço do bocal. (Fig3)
- Première étape: Tuyères de chauffage, PLA à 200℃ PETG à 230℃. (Fig1)
- Étape 2: fermer les canaux inutilisés au moyen d'un outil de nettoyage d'extrémité thermique. (Fig4)
- Étape 3: couper le fil avec un coupe - lames. (Fig5)
- Étape 4: appuyer sur la poignée du four d 'extrusion et insérer le fil dans l' extrémité chaude. (Fig6)
- Étape 5: répéter les étapes 3 et 4 si plusieurs filaments doivent être chargés simultanément
- Étape 6: Extruder les filaments de toutes les extrudeuses jusqu 'à ce qu' ils sortent des orifices de buse. (Fig3)

# How to load/unload filament

## MENU>>temperature


PLA: 200
PETG: 230
MENU>>Motion>>Move axis | (Fig1)
M3 hotend = 3 M4 hotend = 4 | 30 ~ 100

## (Fig 2)

## (Fig 3)

# How to load/unload filament


(Fig 4) | (Fig 5)

## (Fig 6)

50mm

## Enter 50mm

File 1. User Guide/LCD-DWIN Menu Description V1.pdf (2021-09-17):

# Introduction of 4.3-inch TFT screen(DWIN)

V1.0


Operation and Function
Operation | Function
Clockwise rotation | Menu item+ / Value +
Counterclockwise rotation | Menu item+ / Value - Push
Enter/Return Menu,or setting Value

### LCD screen and Keypad

### State main menu description


fig | Description | Remark
1 | Auto shutdown time remaining | Shut down in 15 minutes
2 | Company logo
3 | Enter Print
4 | Print Prepare
5 | Print Control
6 | Printer Information
7 | Current / Target temperature of hot end | This 4 items are always
Current / Target temperature of hot bed | displayed. 8
9 | Current Feedrate percentage
10 | Current z-axis offset

### Prepare menu description


menu | Description | Remark
Back | Return to main menu
Auto Home | Home X/Y/Z or Home All | If Home X or Home All, First Home Y
Move | Move X/Y/Z/E-axis motor
Disable Steppers | Release all motors
Bed Leveling | Hot bed leveling
Power Outage | Turn off the power
Z-Offset | Current Z-axis offset
Prepare PLA | Preheat PLA according to set value
Prepare ABS | Preheat ABS according to set value
Cooldown | Cool the hot bed and hot end, shut down the fan
Language | Language choice | Available in 5 languages

### Control menu description


menu | Description | Remark
Back | Return to main menu
Temperature | Hot bed / hot end temperature, fan speed, PLA / ABS temperature setting
Motion | Feedrate/acceleration/Jerk/Step setting
Mixer | Color mixing settings
Configure | Related function settings
BLTouch | 3D Touch setting | If 3D touch is enabled
Store | Save settings
Load | Load settings
Restore Defauits | Restore default
Info | printer information

### State print menu description


fig | Description | Remark
1 | Printed file name
2 | Progress of printing
3 | Extruder percentage
4 | Printing time
5 | Time remaining
6 | Print tune | Double click to enter Babysteps
7 | Print pause
8 | Print stop
9 | Mixer mode | mix/gradient/random

### Tune menu description


menu | Description | Remark
Back | Return to print menu
Speed | Print speed setting
Hotend Temp | Hotend Temperature setting
Bed Temp | Hotbed Temperature setting
Fan Speed | Fan Speed setting
Z-Offset | Z-axis offset settings
Mixer | Color mixing settings

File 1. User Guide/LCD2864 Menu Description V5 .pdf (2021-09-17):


# Brief of LCD Menu ZONESTAR 3D Printer DIY Kit

# (Base on Marlin 2.0.x)

# Ver: 5


# LCD screen and Keypad

LCD12864 with knob

## Operation and Function

Operation | Function
Clockwise rotation | Menu item+ / Value +
Counterclockwise rotation | Menu item+ / Value -
Push | Open Menu /Enter


fig | Description
1 | Current hotend temperature
2 | Setting hotend temperature
3 | Current hotbed temperature
4 | Setting hotbed temperature
5 | Current X Y Z position
6 | Extrude fan speed
7 | Multiple of print speed
8 | SD card print progress
9 | Status message
10 | mix rate of extruders
11 | Current Virual Tool Number or Auto Mix Mode

State menu description

# Menu description

Menu | Sub-Menu | Description | Remark
| Info Screen | Return to info menu
| Motion | Prepare Menu | Only shows on ideal status
| Pause Print | Pause Printing | Only shows on printing
| Stop Print | Stop Printing | Only shows on printing
| Tune | Tune parameter when printing | Only shows on printing/Motion
| Temperature | Control Menu
| Mixer* | Mixing Settings | Only available in mixing printer.
| Configuration | Set the printer parameter
| Change Filament | A wizard to help change filament
| About printer | Printer infomations
| Change Media | Press it before remove the SD card from control board | Only shows on ideal status
| Switch Power off | Power off the printer (only control board) | Only available has power button
| Print From Media | Press it to start to print from SD card. | Only shows on ideal status
Pop Menu | Babystep Z | double click the knob to open when printing | Only available when printing

Main Menu

*:

# Menu description

Motion

| Move Axis | Move X/Y/Z/Extruder motor | Need to heat nozzle before moving extruder
| Auto HOME | Do homing for all X/Y/Z
| HOME X/Y/Z | Homing X/Y/Z separately
| Level Corners | Move the nozzle to near the corners of hotbed | Adjust the screws under the bed to level it
| Catch Z probe offset | Catch the probe Z offset
| Level bed | Do a bed auto levling processing | Only for bed leveling sensor installed
| Probe Z offset | Adjust probe Z offset
| Bed leveling: Off(ON) | If a Bed leveling has done | Apply the Z axis error when show “ON”
| Disable Motor | Turn off the power of stepper motors
Temperature | Nozzle | Set nozzle temperature
| Bed | Set bed temperature
| Fan Speed | Set extruder FAN speed | Cooling fan is control automatically
| Preheat PLA/ABS | Preheat the hotbed and/or hotbed
Mixer | Active V tool | Set the current work V Tool | These menu only showed when the printer has mixing feature, about the detail, please refer to
| | Set Mixing parameter setting | the mixing feaure user guide. Mix
| Gradient: disable | Set Gradient mixing parameters
| Random Mix: disable | Set Random mixing parameters

# Menu description

Configuration

| Advanced Settings
| Run out sensor: On/Off | Turn on/off the filament run out detection feature | * Refer to “Filament Run out feature”
| Outage Recovery: On/Off | Turn on/off power loss recover feature | * Refer to “Power loss Resume feature”
| Preheat PLA/ABS Conf | Set preheat parameters
| Store Settings | Store the configuration to NVRAM of control board | Do it after you modified parameter!
| Load Settings | Load the NVRAM setting to the printer
| Restore Default | Reset the setting to the default
Tune | Speed | Adjust the print speed | Percentage of speed based on gcode
| Nozzle | Nozzle temperature
| Bed | Hotbed temperature
| Fan Speed | Extruder fan speed
| Flow | Extruder flow rate | Percentage of flow value based on gcode
| Babystep Z | Fine tune the Z height

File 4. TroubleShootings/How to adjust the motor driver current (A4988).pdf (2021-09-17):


56

WARNING!! Please pay attention to the direction of the motor driver module, incorrect direction will damage the control board!!!!

You may need to adjust the drive current because a couple of reasons, for example, difference of the stepper motors, the hot bed weight, etc., you can rotate the potentiometer on the driver module to adjust the current.
NOTE: Too small drive current may cause lost step or abnormal noise. Too big current may damage the driver module because it is over heat!
Recommended current of stepper motors:
X Y& Z motor: 0.8A
Extruder motor: 0.6A (for Titan extruders)
If you want to adjust the current of the motor driver module, please measure the voltage (Vref) on the potentiometer with a multimeter (as below picture), DC Voltage Gears.
For 4988 driver module:
I motor = Vref * 1 . 25

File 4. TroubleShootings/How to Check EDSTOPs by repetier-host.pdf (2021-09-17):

## Check ENDSTOPs by Repetier-Host

Prepare:
Step 1: Install Repetier-host to your PC (NOTE: DONOT USE Repetier-Severice)
Step 2: Connect the printer to PC by USB cable.
Step 3: Set the communication setting, then click connect button on Repetier-host.

About these steps, please refer to the Repetier-host user guide in the SD card. Download link: https://www.jianguoyun.com/p/DdgqMLMQyoP1BxjC56cD

Click Log to open the log window; Choose Manual Control , input M119 and then click send

## Check ENDSTOPs by Repetier-Host


Then you can see the ENDSTOP status in the LOG window

Press the ENDSTOP by hand and check if it can work well

Doesn’t click | Clicked

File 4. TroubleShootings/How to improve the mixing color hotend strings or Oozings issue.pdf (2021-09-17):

# How to improve the Mixing Color


# hotend Stringing/Oozing issue

Step 2: Set Auto-Retract to On , and set the relevant parameters such as Retraction distance and Retraction speed.
Step 1: Load the filaments to all the extruders.
PS1: You can load filaments only two extruders too. The more channels you load filaments, the effect if the better.
PS2: The channel without filaments should be closed with hot end clean tool.

How to improve the M3/M4 hotend stringing or Oozing


Retract mm: 8~10 | Unretr. mm: 0
Retract V: 10~20 | Unretr. mm: 8~15
Hop mm: 0~1 (set to 0 if you have set the Z hop in slicing setting)

You can also add a M209 command in the “start gcode” of slicing software
1.Add a “M209 S1” command on the start code
2.Enable Retraction and set the retraction distance to 8~10mm and retraction speed to 30mm/s

How to improve the Mixing Color hotend stringing or Oozing


### Cura


### Simplify 3D

How to improve the Mixing Color hotend stringing or Oozing

### Repetier-HOST

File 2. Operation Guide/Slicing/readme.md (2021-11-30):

The newest slicing guide, please refer to the below link:
https://github.com/ZONESTAR3D/Slicing-Guide    
[**slicing guide**](https://github.com/ZONESTAR3D/Slicing-Guide)

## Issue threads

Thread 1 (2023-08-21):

The download link for Cura printing profiles is broken (/Slicing-Guide/cura)

doomducker, 2023-08-21:
i am unable to download the printing profiles for Cura when looking at the slicing guide meaning i cannot use my 3d printer.

How to Recreate this Bug:
<ol>
  <li>go to the cura slicing guide https://github.com/ZONESTAR3D/Slicing-Guide/tree/master/cura.  </li>
  <li>find step 1</li>
  <li>ubove the first video/GIF you should see this line
  "Download [⬇️ Zonestar 3D Printer Profiles.](https://github.com/ZONESTAR3D/Slicing-Guide/blob/master/cura/ZONESTAR_Cura_Resources.zip) 👈Click here and then click "download" button. the last updata on 2022-09-19.."</li>
  <li>click on the link where it says  " Zonestar 3D Printer Profiles. " (https://github.com/ZONESTAR3D/Slicing-Guide/blob/master/cura/ZONESTAR_Cura_Resources.zip)</li>
  <li> this should result in a github error 404 page</li>
  <li> you have now recreated my issue.</li>
  </ol>

  extra information
  windows 11
  firefox 116.0.3 (64bit)"
  github webpage
3d printer zonestar Z8T
